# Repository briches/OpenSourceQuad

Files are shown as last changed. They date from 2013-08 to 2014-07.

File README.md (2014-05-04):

<b>OpenSourceQuad</b>
==========

<b>Author</b>: Brandon Riches<br />

Started in May of 2013, and always a work in progress! <br />

Feel free to <b>[fork](https://github.com/briches/OpenSourceQuad/fork)</b> the repo and submit a pull request.  

Released under the GNU Public License  

<b>Programming the flight controller:</b>  
----

(Finally) <b>Safe Fuse Bytes</b>  
<code>lfuse = 0xD6, hfuse = 0xB1, efuse = 0xfd</code>  

<b>Using arduino avrisp:</b>  
<code>avrdude -P comport -b 19200 -c avrisp -p m2560 -v -e -U flash:w:hexfilename.hex</code>  
<b>Using USBasp</b>  
<code>avrdude -c usbasp -p m2560 -v -e -U flash:w:tmp.hex</code>  
<b>Writing fuse bits</b>  
<code>avrdude -c usbasp -p m2560 -U hfuse:w:0xB1:m -U lfuse:w:0xD6:m -U efuse:w:0xFD:m</code>

<b>ESC Settings</b>  
- Batt Type: LiXX
- Cut off: high
- Cut off Type: hard
- Brake: off
- Timing: auto
- Start up: medium

Description
-----------

Quadcopter flight firmware! 

The end goal is to create future proof, easy-to-use 
and customizable firmware for any flight configuration ( which is quite the lofty goal, but I'm working on it).
<br /><br />

<br />
Sensors:
 - LSM303 Accelerometer / Magnetometer 
 - MPU3050 Gyro
 - Adafruit ultimate GPS module
 - Maxbotix USRF (LV-EZ1)
 - BMP085 Barometeric Pressure/Temperature/Altitude

Features and long term goals:
----------------------------
   <br />
  - Fully autonomous takeoff and landing. Has the option to be controlled via radio comms. <br />

  - 9DOF sensor module (IMU) with GPS and localization  <br />
  
  - Open source =]
   <br />
   <br />

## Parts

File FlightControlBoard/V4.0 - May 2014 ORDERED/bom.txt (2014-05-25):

Qty,Value,Device,Package,Parts,,,,Description,PROD_ID
4,LED,LED0603,LED-0603,"5_PWR, DIO1, HB, RSSI",,,,LEDs,
1,,M03LOCK,1X03_LOCK,USRF,,,,Header 3,
8,,PINHD-1X3,1X03,"M1, M2, M3, M4, SEL1, SEL2, SEL3, SEL4",,,,PIN HEADER,
1,500ma,PTCFUSE-1812,1812,F1,,,,"PTC fuses, resettable thermi",stors
1,0.22u,CAP0402-CAP,0402-CAP,C11,,,,Capacitor,
8,100n,CAP0402-CAP,0402-CAP,"C1, C2, C3, C4, C5, C","6,","C8,",C14,Capacitor,
4,10K,RESISTOR0402-RES,0402-RES,"R3, R18, R20, R24",,,,Resistor,
7,10k,RESISTOR0402-RES,0402-RES,"R9, R12, R15, R16, R1","9,",R22,", R23",Resistor,
1,10n,CAP0402-CAP,0402-CAP,C16,,,,Capacitor,
4,1K,RESISTOR0402-RES,0402-RES,"R1, R2, R5, R7",,,,Resistor,
1,1M,RESISTOR0402-RES,0402-RES,R8,,,,Resistor,
4,1k,RESISTOR0402-RES,0402-RES,"R4, R6, R13, R17",,,,Resistor,
4,4.7k,RESISTOR0402-RES,0402-RES,"R10, R11, R14, R21",,,,Resistor,
2,4.7u,C-EUC3216,C3216,"C12, C13",,,,"CAPACITOR, European symbol",
3,4.7u,CAP0402-CAP,0402-CAP,"C7, C9, C10",,,,Capacitor,
1,470n,CAP0402-CAP,0402-CAP,C15,,,,Capacitor,
1,ATMEGA2560AU,ATMEGA2560AU,TQFP100,U4,,,,Atmel 100-pin 8-bit uC,
1,AVR_SPI_PROG,AVR_SPI_PROG,AVR_ICSP,ICSP,,,,AVR 10-pin ICSP Header,
1,BMP085,BMP085,BMP085,BMP1,,,,BMP085 Pressure Sensor Great,little MEMS pressure sensor. SKU: COM-09603
8,ESC_CONN,ESC_CONN,ESC_CONN,"+, -, GND, U$3, U$4,",U$,"5, U","$6, V+",,
1,HEX_CONVERTER,HEX_CONVERTER,SO016,U2,,,,Just what it says.,
1,JST_XH_4,JST_XH_4,JST-XH4,JP1,,,,,
1,L3G4200D,L3G4200D,LGA16-4X4,U5,,,,"L3G4200D Three-axis, digital",output gyroscope
1,LS20031,LS20031,LS20031,U$1,,,,,
1,LSM303DLHSMD,LSM303DLHSMD,LGA28-5X5,U3,,,,I2C accelerometer/magnetomet,er/tilt compensated compass
6,MOSFET,MOSFET-NCHANNELBSS138,SOT23,"Q1, Q2, Q3, Q4, Q5, Q",6,,,Common NMOSFET Parts,TRANS-00830
1,NCP1117,NCP1117,DPAK,REG1,,,,,
1,RESONATOR,RESONATORMU,RESONATOR,CSTCE16MOV53-RO16MHZ,,,,,
2,SCHOTTKY-1206,D1206            SCHOTTKY-1206D1206,C1206,"D2, D3",,,,,
1,SWITCH-MOMENT,ARY-2-SMD-1101NE SWITCH-MOMENTARY-2-SMD-1101NE,TACTILE-SWITCH-1101NE,RST,,,,Various NO switches- pushbut,"tons, reed, etc"
1,USD-SOCKETNEW,USD-SOCKETNEW,MICRO-SD-SOCKET-PP,U1,,,,microSD Socket,
1,V_REG_LDOSMD,V_REG_LDOSMD,SOT23-5,1.8VREG,,,,Voltage Regulator LDO,
1,XBEE-1B3,XBEE-1B3,XBEE-SMD,U$2,,,,Xbee module footprints,CONN-09042
,,,,,,,,,
,,,,,,,,,
,Qty,Part Number,Manufacturer,Package,Reference,Description,Digi-Key P/N,Mouser P/N,Newark P/N
Capacitors,,,,,,,,,

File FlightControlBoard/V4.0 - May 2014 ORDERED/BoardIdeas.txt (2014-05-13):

Problems with V3.0
1. Board is pretty large - Made 7x7 cm
2. Trace width inconsistant
3. 3V3 Reg incorrectly routed
4. Servo leads incorrectly routed
5. Capacitor on 1.8V reg output
6. Barometeric sensor, make adaptable between BMP180 and BMP085
7. Include power connections on board!!

V3.1
Layers
Top. Normal Traces w/ GND Plane
Route2. Normal Traces w/ GND Plane
Route15. AGND Plane, no traces!
Bottom. +Vbatt Plane

Need to route GND planes around power connections
 - allow adequate spacing

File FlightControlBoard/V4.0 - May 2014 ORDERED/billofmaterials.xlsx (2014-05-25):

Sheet: bom_quadcopter
Quantity | Part | Optional | Approx. price per | Total
1 | Frame | 0 | $50.00 | $50.00
4 | Speed Controllers (ESC) | 0 | $15.00 | $60.00
4 | Motors, Brushless | 0 | $20.00 | $80.00
1 | Battery, LiPo | 0 | $40.00 | $40.00
4 | Propellors | 0 | $1.00 | $4.00
1 | Power distribution method | 0 | $5.00 | $5.00
1 | Control board | 0 | $100.00 | $100.00
1 | Ultrasonic range finder | 1 | $20.00 | $20.00
1 | Xbee Radio Module | 1 | $20.00 | $20.00
1 | GPS | 1 | $40.00 | $40.00
1 | microSD card | 1 | $15.00 | $15.00
 |  |  | Min | Max
 |  | Total | $339.00 | $434.00

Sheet: bom_board.xlsx
 | Bill of materials for Open Source Quad Control Board Rev 4. |  |  |  |  |  |  |  | PROD_ID
Capacitors
 | Quantity | Part | Value | Device | Package | Description | Digikey P/N | Manufacturer
 | 1 | C16 | 10nF | CAP0402-CAP | 402 | ceramic | 445-7386-1-ND | TDK Corporation
 | 10 | C1, C2, C3, C4, C5, C6, C8, C9, C14, C17 | 100nF | CAP0402-CAP | 402 | ceramic | 445-7348-1-ND | TDK Corporation
 | 1 | C11 | 220nF | CAP0402-CAP | 402 | ceramic | 445-5944-1-ND | TDK Corporation
 | 1 | C15 | 470n | CAP0402-CAP | 402 | ceramic | 445-10972-1-ND | TDK Corporation
 | 2 | C7, C10 | 4.7uF | CAP0402-CAP | 402 | ceramic | 445-10914-1-ND | TDK Corporation
 | 3 | C12, C13, C18 | 10uF | CAP_POL1206 | EIA3216 | polarized | 399-5152-1-ND | Kemet
Resistors
 | Quantity | Part | Value | Device | Package | Description | Digikey P/N | Manufacturer
 | 10 | R1, R2, R4, R5, R6, R7, R13, R17, R25, R26 | 1k | RESISTOR0603-RES | 603 | resistor | CR0603-JW-102ELFCT-ND | Bourns Inc.
 | 4 | R10, R11, R14, R21 | 4.7k | RESISTOR0603-RES | 603 | resistor | CR0603-JW-472ELFCT-ND | Bourns Inc.
 | 11 | R3, R9, R12, R15, R16, R18, R19, R20, R22, R23, R24 | 10k | RESISTOR0603-RES | 603 | resistor | CR0603-JW-103ELFCT-ND | Bourns Inc.
 | 1 | R8 | 1M | RESISTOR0603-RES | 603 | resistor | CR0603-JW-105ELFCT-ND | Bourns Inc.
Connectors
 | Quantity | Part | Value | Device | Package | Description | Digikey P/N | Manufacturer
 | 1 | 5x2 ICSP Header |  |  | 500 |  | 952-2380-ND | Harwin Inc.
 | 1 | SMT XH 4 pos connector |  |  | XH |  | 455-2262-1-ND | JST Sales America
 | 2 | Xbee header |  |  |  |  | S5751-10-ND | Sullins Connector
 | 1 | .1 " header 36 pos |  |  |  |  | WM50014-36-ND | Molex Inc.
 | 1 | CONN MINI MICRO-SD 8PIN PCB GOLD |  |  |  |  | 101-00660-68-6-1-ND | Amphenol Commer
 | 1 | CONN USB MINI B R/A SMD |  |  |  |  | ED2992CT-ND | On Shore
 | 4 | Jumper |  |  |  |  | 3M9580-ND | 3M4
Diodes
 | Quantity | Part | Value | Device | Package | Description | Digikey P/N | Manufacturer
 | 3 | HB, DIO1, RX | RED | LED0603 | 603 |  | 160-1436-1-ND | Lite-On Inc
 | 1 | TX | YELLOW | LED0603 | 603 |  | 160-1437-1-ND | Lite-On Inc
 | 2 | RSSI, 5_PWR | GREEN | LED0603 | 603 |  | 160-1435-1-ND | Lite-On Inc
 | 2 | SD1206 |  | SCHOTTKY-1206D1206 | 1206 |  | 478-7804-1-ND | AVX Corporation
Resonators
 | Quantity | Part | Value | Device | Package | Description | Digikey P/N | Manufacturer
 | 1 | CSTCE16M0V53-R0 | 20MHz |  | 3-SMD |  | 490-1198-1-ND | Murata
Fuses
 | Quantity | Part | Value | Device | Package | Description | Digikey P/N | Manufacturer
 | 1 | F1 | PTC_FUSE | PTCFUSE-1812 | 1812 |  | MF-MSMF050-2CT-ND | Bourns Inc.
MOSFETs
 | Quantity | Part | Value | Device | Package | Description | Digikey P/N | Manufacturer
 | 6 | Q1, Q2, Q3, Q4, Q5, Q6 | BSS | MOSFET-NCHANNELBSS138 | SOT23 |  | BSS138CT-ND | Fairchild Semi
Switch
 | Quantity | Part | Value | Device | Package | Description | Digikey P/N | Manufacturer
 | 1 | RST |  |  | TACTILE-SWITCH-1101NE |  | 401-1705-1-ND | C&K Components
IC's
 | Quantity | Part | Value | Device | Package | Description | Digikey P/N | Manufacturer
 | 1 | U7 | FT232RLSSOP |  | 28-SSOP | USB-RS232 | 768-1007-1-ND | FTDI
 | 1 | U5 | L3G4200D |  | LGA16-4X4 | gyro | 497-11071-1-ND | ST
 | 1 | U4 | ATMEGA2560AU | ATMEGA2560AU | TQFP100 | MCU | ATMEGA2560-16AU-ND | Atmel
 | 1 | U3 | LSM303DLHSMD |  | LGA28-5X5 |  | 497-10765-1-ND | ST
 | 1 | U2 | HEX_CONVERTER |  | 16-SOIC N | logic level | 296-31503-1-ND | TI
 | 1 | REG1 | NCP1117 |  | DPAK | 3.3V reg | NCP1117DT33RKGOSCT-ND | ON Semi
 | 1 | 1.8VREG | V_REG_LDOSMD |  | TSOT-23-5 | 1.8V reg | 296-17778-1-ND | TI
 | 1 | BMP085 | Pressure Sensor |  |  |  | N/A
 | 1 | XB24-API-001 | Xbee |  |  |  | 602-1273-ND
 | 1 | LS20031 | GPS

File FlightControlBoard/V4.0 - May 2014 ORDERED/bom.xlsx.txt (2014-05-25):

Capacitors															
	Quantity	Part	Value	Device	Package	Description	Part Number								PROD_ID
	1	C16	10nF	CAP0402-CAP	0402-CAP	Capacitor									
	10	"C1, C2, C3, C4, C5, C6, C8, C9, C14, C17"	100nF	CAP0402-CAP	402	ceramic									
	1	C11	220nF	CAP0402-CAP	402	ceramic									
	1	C15	470n	CAP0402-CAP											
	2	"C7, C10"	4.7uF	CAP0402-CAP	402	ceramic	445-10914-1-ND								
	3	"C12, C13, C18"	10uF	CAP_POL1206	EIA3216	polarized									

Resistors

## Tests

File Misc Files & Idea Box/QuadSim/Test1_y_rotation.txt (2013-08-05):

Test ID: 1.0

Total Mass: 1.1
Moments of Inertia: [0.0089, 0.0098, 0.0187]
Thrust: 0.15
Current Draw: [5, 18]
Battery Capacity: 2450
Rotational DoF axis: [0, 1, 0]
Translational DoF axis: [0, 0, 0]

This test is constrained to have only rotation about the y-axis,
as in our test apparatus. 
Most of these values are guesses still.

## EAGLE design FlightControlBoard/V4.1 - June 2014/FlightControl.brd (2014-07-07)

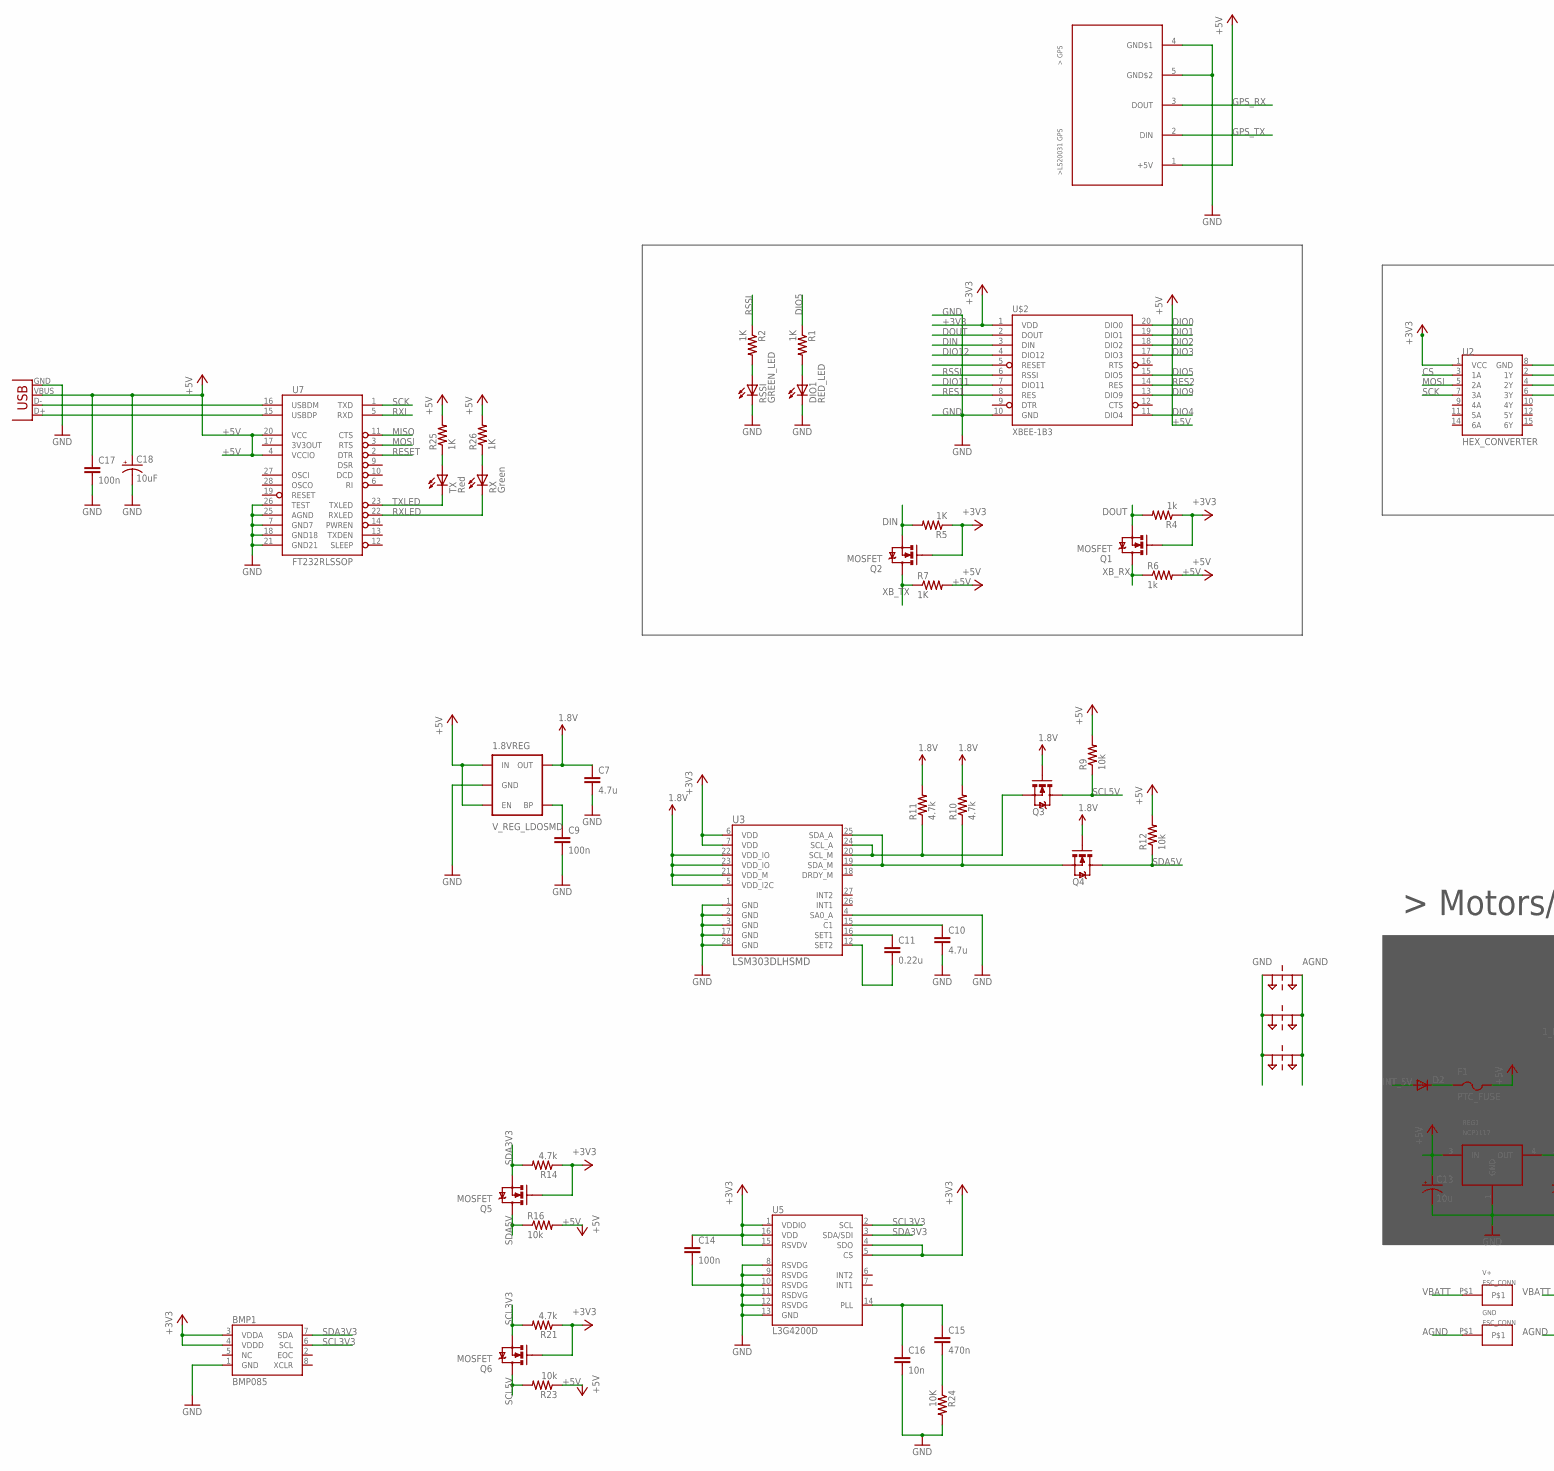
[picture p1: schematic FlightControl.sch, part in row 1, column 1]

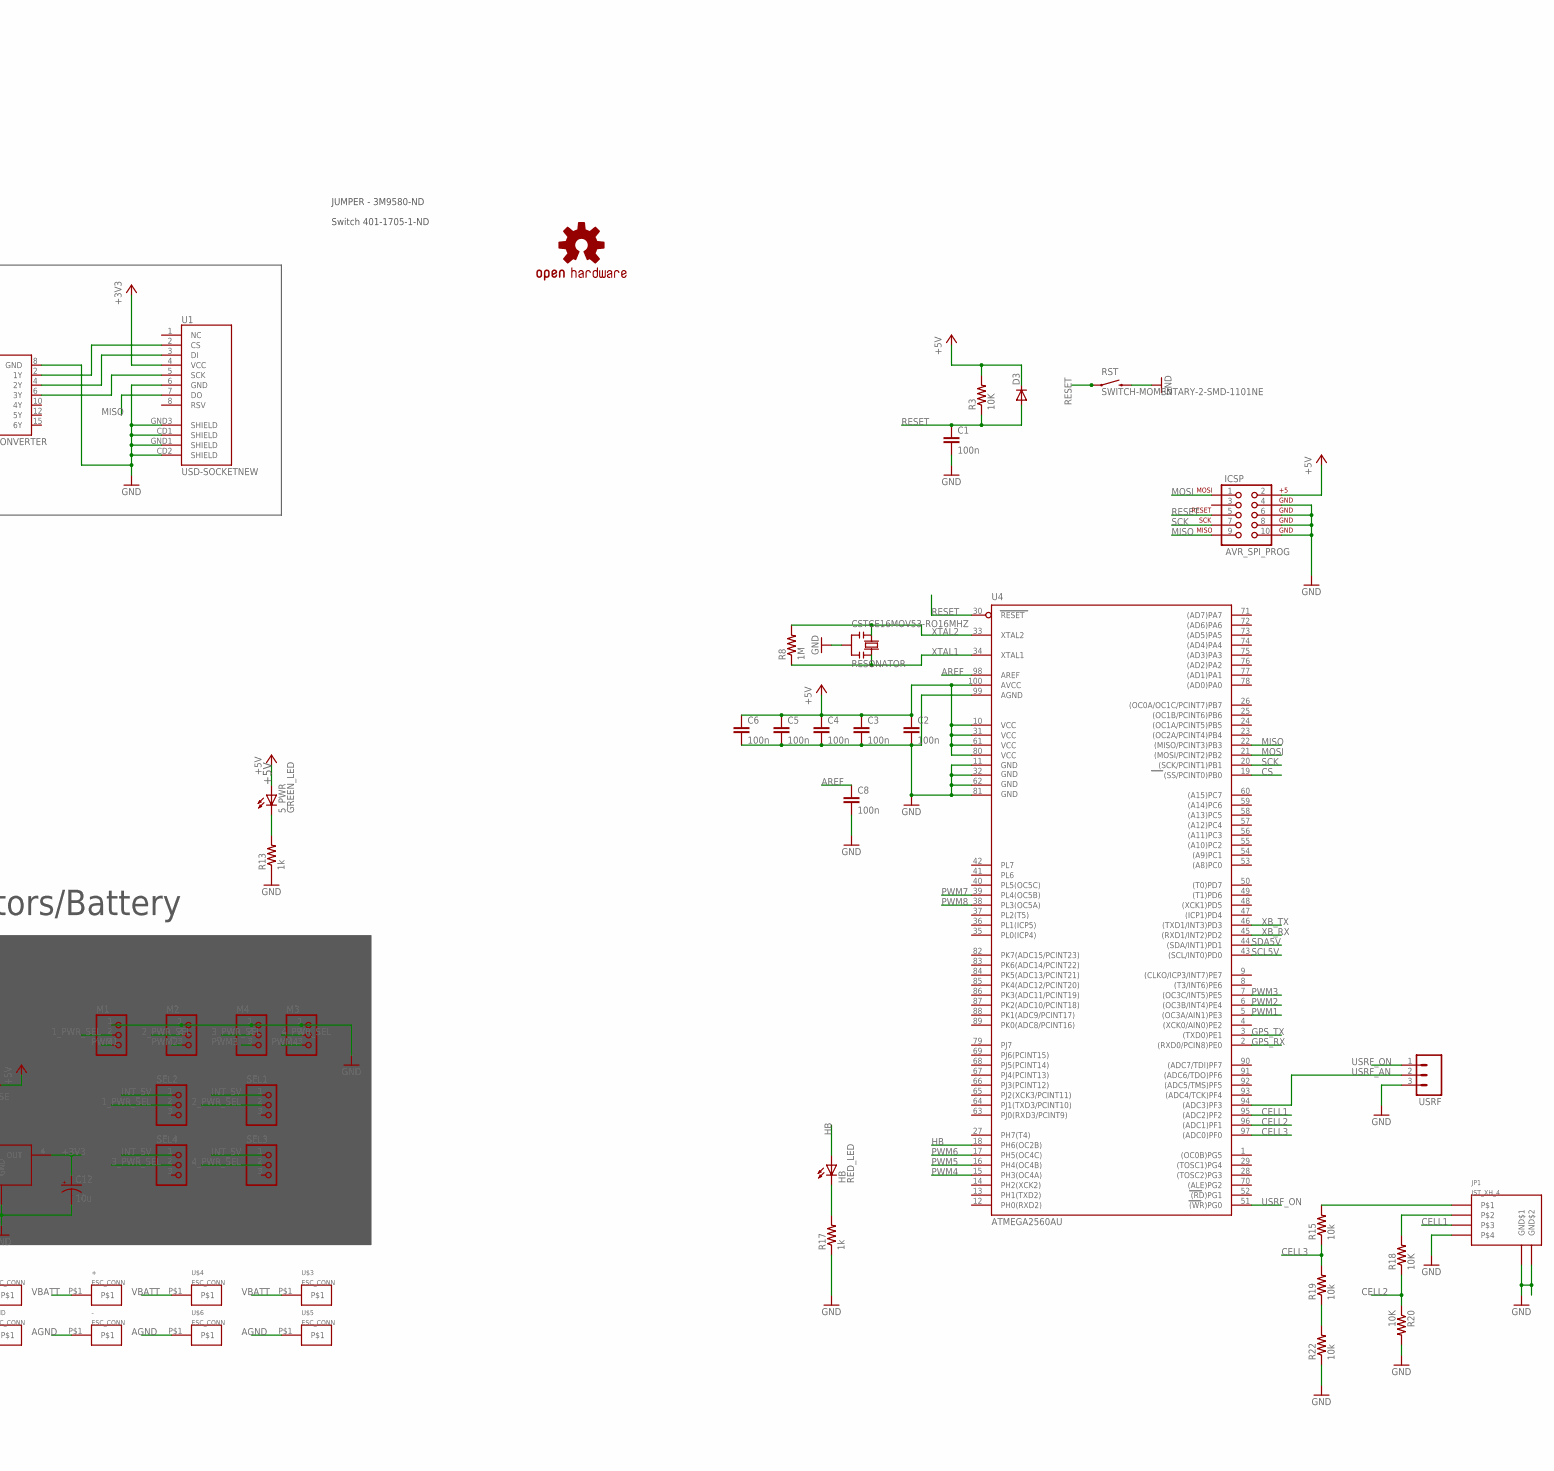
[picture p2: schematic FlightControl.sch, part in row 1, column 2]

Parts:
1.8VREG: V_REG_LDOSMD; SOT23-5
5_PWR: GREEN_LED; LED-0603
+: ESC_CONN
-: ESC_CONN
BMP1: BMP085
C1, C2, C3, C4, C5, C6, C8, C9, C14, C17: 100n; 0402-CAP
C7, C10: 4.7u; 0402-CAP
C11: 0.22u; 0402-CAP
C12, C13: 10u; EIA3216
C15: 470n; 0402-CAP
C16: 10n; 0402-CAP
C18: 10uF; EIA3216
CSTCE16MOV53-RO16MHZ: RESONATOR
D2, D3: SCHOTTKY-1206D1206; C1206
DIO1: RED_LED; LED-0603
F1: PTC_FUSE; 1812
GND: ESC_CONN
HB: RED_LED; LED-0603
ICSP: AVR_SPI_PROG; AVR_ICSP
JP1: JST_XH_4; JST-XH4
LOGO1: OSHW-LOGOL; OSHW-LOGO-L
M1, M2, M3, M4: PINHD-1X3; 1X03
PT1, PT2, PT3: 2PT_GND_TIE
Q1, Q2, Q3, Q4, Q5, Q6: MOSFET; SOT23
R1, R2, R5, R7, R25, R26: 1K; 0603-RES
R3, R18, R20, R24: 10K; 0603-RES
R4, R6, R13, R17: 1k; 0603-RES
R8: 1M; 0603-RES
R9, R12, R15, R16, R19, R22, R23: 10k; 0603-RES
R10: 4.7k; 0402-RES
R11, R14, R21: 4.7k; 0603-RES
REG1: NCP1117; DPAK
RSSI: GREEN_LED; LED-0603
RST: SWITCH-MOMENTARY-2-SMD-1101NE; TACTILE-SWITCH-1101NE
RX: Green; LED-0603
SEL1, SEL2, SEL3, SEL4: PINHD-1X3; 1X03
TX: Red; LED-0603
U1: USD-SOCKETNEW; MICRO-SD-SOCKET-PP
U2: HEX_CONVERTER; SO016
U3: LSM303DLHSMD; LGA28-5X5
U4: ATMEGA2560AU; TQFP100
U5: L3G4200D; LGA16-4X4
U7: FT232RLSSOP; SSOP28DB
U$1: LS20031
U$2: XBEE-1B3; XBEE-SMD
U$3, U$4, U$5, U$6: ESC_CONN
USRF: M03LOCK; 1X03_LOCK
V+: ESC_CONN
X2: USB-SMD-NS; USB-MINIB-NOSTOP

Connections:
1.8V: 1.8VREG.5 (OUT), C7.1, Q3.1 (G), Q4.1 (G), R10.2, R11.2, U3.5 (VDD_I2C), U3.21 (VDD_M), U3.22 (VDD_IO), U3.23 (VDD_IO)
1_PWR_SEL: M1.2, SEL2.2
2_PWR_SEL: M2.2, SEL1.2
3_PWR_SEL: M4.2, SEL4.2
4_PWR_SEL: M3.2, SEL3.2
+3V3: BMP1.3 (VDDA), BMP1.4 (VDDD), C12.A (+), C14.1, Q1.1 (G), Q2.1 (G), Q5.1 (G), Q6.1 (G), R4.1, R5.1, R14.1, R21.1, REG1.4 (OUT), U1.4 (VCC), U2.1 (VCC), U3.6 (VDD), U3.7 (VDD), U5.1 (VDDIO), U5.4 (SDO), U5.5 (CS), U5.15 (RSVDV), U5.16 (VDD), U$2.1 (VDD)
+5V: 1.8VREG.1 (IN), 1.8VREG.3 (EN), 5_PWR.A, C2.1, C3.1, C4.1, C5.1, C6.1, C13.A (+), C17.1, C18.A (+), D3.2 (C), F1.2, ICSP.2, R3.2, R6.2, R7.2, R9.2, R12.2, R16.2, R23.1, R25.2, R26.2, REG1.3 (IN), U4.10 (VCC), U4.31 (VCC1), U4.61 (VCC2), U4.80 (VCC3), U4.100 (AVCC), U7.4 (VCCIO), U7.20 (VCC), U$1.1 (+5V), X2.VBUS
AGND: -.P$1, GND.P$1, PT1.P$2, PT2.P$2, PT3.P$2, U$5.P$1, U$6.P$1
AREF: C8.1, U4.98 (AREF)
CELL1: JP1.P$3, U4.95 ((ADC2)PF2)
CELL2: R18.1, R20.1, U4.96 ((ADC1)PF1)
CELL3: R15.1, R19.2, U4.97 ((ADC0)PF0)
CS: U2.3 (1A), U4.19 ((SS/PCINT0)PB0)
DIN: Q2.2 (S), R5.2, U$2.3 (DIN)
DIO0: U$2.20 (DIO0)
DIO1: U$2.19 (DIO1)
DIO2: U$2.18 (DIO2)
DIO3: U$2.17 (DIO3)
DIO4: U$2.11 (DIO4)
DIO5: R1.1, U$2.15 (DIO5)
DIO9: U$2.13 (DIO9)
DIO11: U$2.7 (DIO11)
DIO12: U$2.4 (DIO12)
DOUT: Q1.2 (S), R4.2, U$2.2 (DOUT)
GND: 1.8VREG.2 (GND), BMP1.1 (GND), C1.2, C2.2, C3.2, C4.2, C5.2, C6.2, C7.2, C8.2, C9.2, C10.2, C12.C (-), C13.C (-), C14.2, C16.2, C17.2, C18.C (-), CSTCE16MOV53-RO16MHZ.2, DIO1.C, ICSP.4, ICSP.6, ICSP.8, ICSP.10, JP1.GND$1, JP1.GND$2, JP1.P$4, M1.1, M2.1, M3.1, M4.1, PT1.P$1, PT2.P$1, PT3.P$1, R13.1, R17.1, R20.2, R22.1, R24.2, REG1.1 (GND), RSSI.C, RST.P$2 (2), U1.6 (GND), U1.CD1 (SHIELD), U1.CD2 (SHIELD), U1.GND1 (SHIELD), U1.GND3 (SHIELD), U2.8 (GND), U3.1 (GND), U3.2 (GND), U3.3 (GND), U3.4 (SA0_A), U3.17 (GND), U3.28 (GND), U4.11 (GND), U4.32 (GND1), U4.62 (GND2), U4.81 (GND3), U4.99 (AGND), U5.8 (RSVDG), U5.9 (RSVDG), U5.10 (RSVDG), U5.11 (RSDVG), U5.12 (RSVDG), U5.13 (GND), U7.7 (GND7), U7.18 (GND18), U7.21 (GND21), U7.25 (AGND), U7.26 (TEST), U$1.4 (GND$1), U$1.5 (GND$2), U$2.10 (GND), USRF.3, X2.GND
GPS_RX: U4.2 ((RXD0/PCIN8)PE0), U$1.3 (DOUT)
GPS_TX: U4.3 ((TXD0)PE1), U$1.2 (DIN)
HB: HB.A, U4.18 (PH6(OC2B))
INT_5V: D2.1 (A), SEL1.1, SEL2.1, SEL3.1, SEL4.1
MISO: ICSP.9, U1.7 (DO), U4.22 ((MISO/PCINT3)PB3), U7.11 (CTS)
MOSI: ICSP.1, U2.5 (2A), U4.21 ((MOSI/PCINT2)PB2), U7.3 (RTS)
unnamed: R19.1, R22.2
unnamed: 1.8VREG.4 (BP), C9.1
unnamed: U1.2 (CS), U2.2 (1Y)
unnamed: U1.3 (DI), U2.4 (2Y)
unnamed: U1.5 (SCK), U2.6 (3Y)
unnamed: C11.1, U3.16 (SET1)
unnamed: 5_PWR.C, R13.2
unnamed: DIO1.A, R1.2
unnamed: R2.2, RSSI.A
unnamed: HB.C, R17.2
unnamed: R25.1, TX.A
unnamed: C11.2, U3.12 (SET2)
unnamed: C10.1, U3.15 (C1)
unnamed: D2.2 (C), F1.1
unnamed: Q3.2 (S), R11.1, U3.20 (SCL_M), U3.24 (SCL_A)
unnamed: Q4.2 (S), R10.1, U3.19 (SDA_M), U3.25 (SDA_A)
unnamed: JP1.P$2, R18.2
unnamed: C15.1, C16.1, U5.14 (PLL)
unnamed: C15.2, R24.1
unnamed: JP1.P$1, R15.2
unnamed: R26.1, RX.A
PWM1: M1.3, U4.5 ((OC3A/AIN1)PE3)
PWM2: M2.3, U4.6 ((OC3B/INT4)PE4)
PWM3: M4.3, U4.7 ((OC3C/INT5)PE5)
PWM4: M3.3, U4.15 (PH3(OC4A))
PWM5: U4.16 (PH4(OC4B))
PWM6: U4.17 (PH5(OC4C))
PWM7: U4.39 (PL4(OC5B))
PWM8: U4.38 (PL3(OC5A))
RES1: U$2.8 (RES)
RES2: U$2.14 (RES)
RESET: C1.1, D3.1 (A), ICSP.5, R3.1, RST.P$1 (1), U4.30 (RESET), U7.2 (DTR)
RSSI: R2.1, U$2.6 (RSSI)
RXI: U7.5 (RXD)
RXLED: RX.C, U7.22 (RXLED)
SCK: ICSP.7, U2.7 (3A), U4.20 ((SCK/PCINT1)PB1), U7.1 (TXD)
SCL3V3: BMP1.6 (SCL), Q6.2 (S), R21.2, U5.2 (SCL)
SCL5V: Q3.3 (D), Q6.3 (D), R9.1, R23.2, U4.43 ((SCL/INT0)PD0)
SDA3V3: BMP1.7 (SDA), Q5.2 (S), R14.2, U5.3 (SDA/SDI)
SDA5V: Q4.3 (D), Q5.3 (D), R12.1, R16.1, U4.44 ((SDA/INT1)PD1)
TXLED: TX.C, U7.23 (TXLED)
USB_D+: U7.15 (USBDP), X2.D+
USB_D-: U7.16 (USBDM), X2.D-
USRF_AN: U4.94 ((ADC3)PF3), USRF.2
USRF_ON: U4.51 ((WR)PG0), USRF.1
VBATT: +.P$1, U$3.P$1, U$4.P$1, V+.P$1
XB_RX: Q1.3 (D), R6.1, U4.45 ((RXD1/INT2)PD2)
XB_TX: Q2.3 (D), R7.1, U4.46 ((TXD1/INT3)PD3)
XTAL1: CSTCE16MOV53-RO16MHZ.3, R8.1, U4.34 (XTAL1)
XTAL2: CSTCE16MOV53-RO16MHZ.1, R8.2, U4.33 (XTAL2)

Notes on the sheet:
JUMPER - 3M9580-ND
Switch 401-1705-1-ND

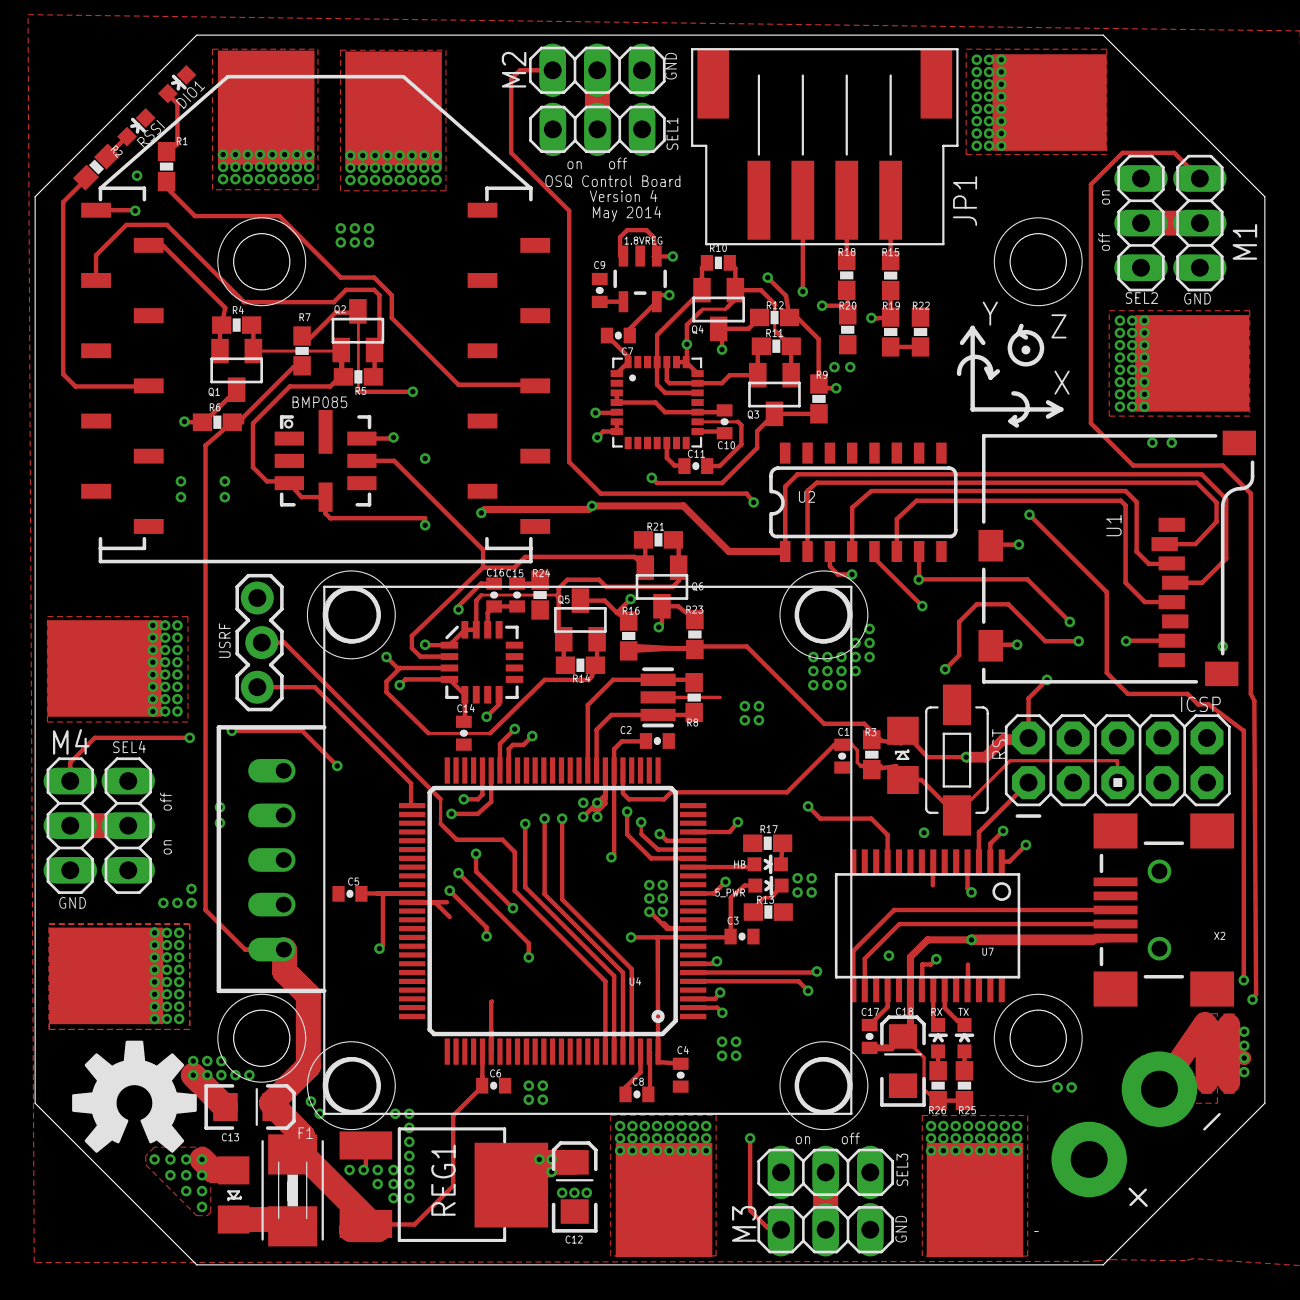
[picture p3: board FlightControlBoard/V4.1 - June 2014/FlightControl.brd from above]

Board: 4 copper layers, 70.0 x 70.0 mm, 96 parts (0 on the bottom side), 66 nets.

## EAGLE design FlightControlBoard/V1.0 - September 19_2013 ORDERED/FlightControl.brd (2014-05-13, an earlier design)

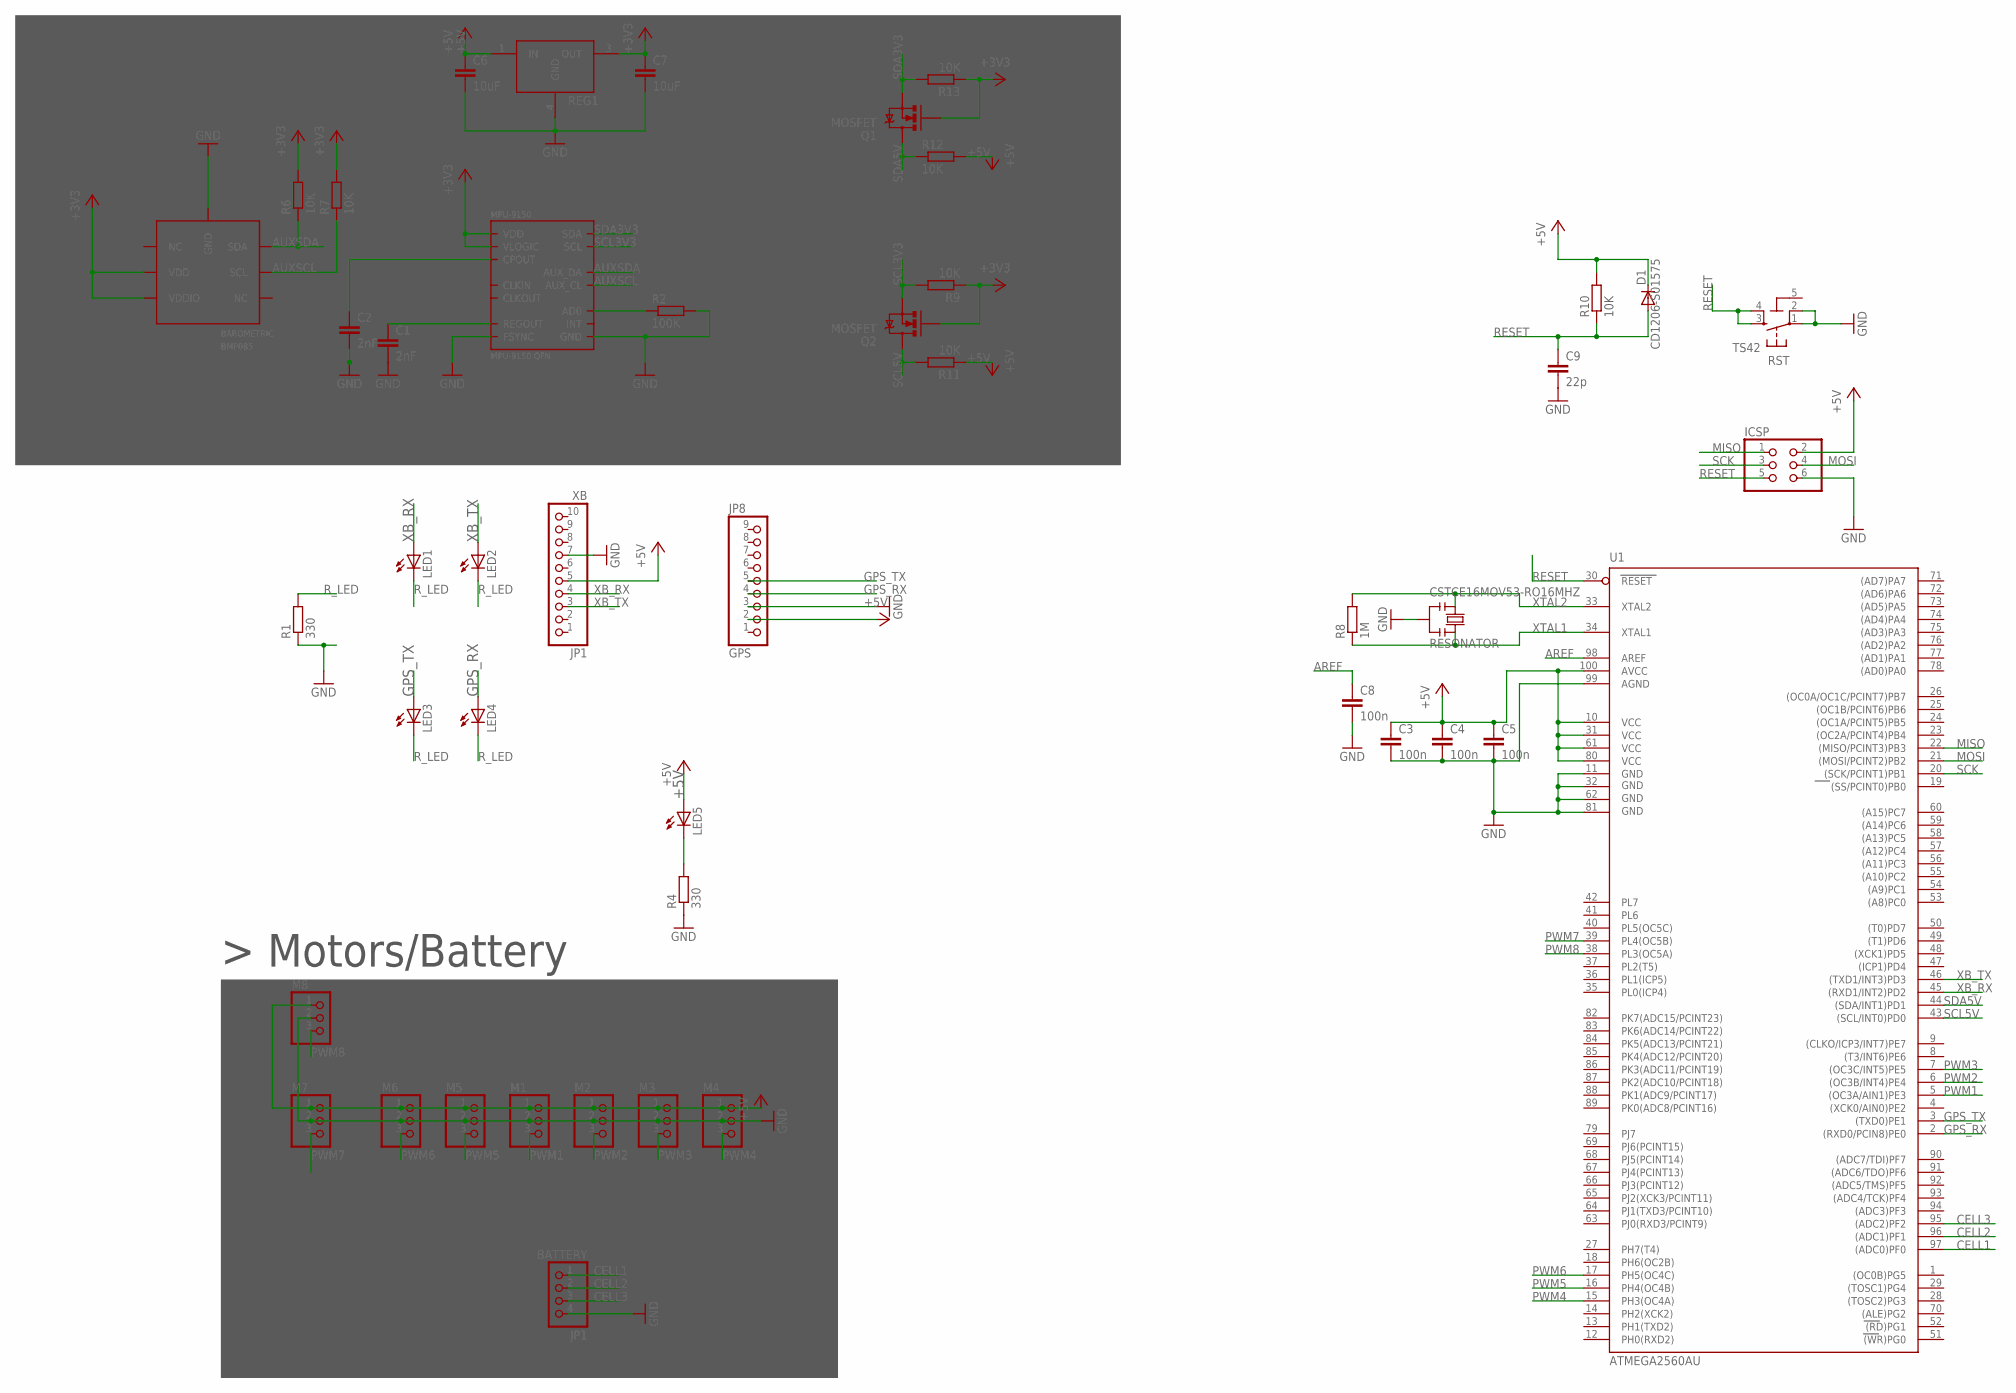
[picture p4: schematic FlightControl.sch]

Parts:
BAROMETRIC: BMP085; 7LGA
BATTERY: JP1; 1X04
C1, C2: 2nF; C0603-ROUND
C3, C4, C5, C8: 100n; C0603-ROUND
C6, C7: 10uF; CAP-PTH-SMALLEZ
C9: 22p; C0603-ROUND
CSTCE16MOV53-RO16MHZ: RESONATOR
D1: CD1206-S01575; MINIMELF
GPS: JP8; 1X09
ICSP: PINHD-2X3; 2X03
JP1: XB; 1X10
LED1, LED2, LED3, LED4, LED5: LEDCHIPLED_1206; CHIPLED_1206
M1, M2, M3, M4, M5, M6, M7, M8: PINHD-1X3; 1X03
MPU-9150: MPU-9150.QFN; QFN.24.4X4
Q1, Q2: MOSFET; SOT23
R1, R4: 330; R0603-ROUND
R2: 100K; R0603-ROUND
R6, R7, R9, R10, R11, R12, R13: 10K; R0603-ROUND
R8: 1M; R0603-ROUND
REG1: LD39300; DPAK
RST: TS42
U1: ATMEGA2560AU; TQFP100

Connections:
5-GND: RST.5 (5-GND)
+3V3: BAROMETRIC.2 (VDD), BAROMETRIC.3 (VDDIO), C7.1, MPU-9150.3 (VDD), MPU-9150.8 (VLOGIC), MPU-9150.13 (VDD), Q1.1 (G), Q2.1 (G), R6.2, R7.2, R9.1, R13.1, REG1.3 (OUT)
+5V: C3.1, C4.1, C5.1, C6.1, D1.C, GPS.2, ICSP.2, JP1.5, LED5.A, M1.1, M2.1, M3.1, M4.1, M5.1, M6.1, M7.1, M8.1, R10.2, R11.1, R12.2, REG1.1 (IN), U1.10 (VCC), U1.31 (VCC1), U1.61 (VCC2), U1.80 (VCC3), U1.100 (AVCC)
AD0: MPU-9150.9 (AD0), R2.1
AREF: C8.1, U1.98 (AREF)
AUXSCL: BAROMETRIC.5 (SCL), MPU-9150.7 (AUX_CL), R7.1
AUXSDA: BAROMETRIC.6 (SDA), MPU-9150.6 (AUX_DA), R6.1
CELL1: BATTERY.1, U1.97 ((ADC0)PF0)
CELL2: BATTERY.2, U1.96 ((ADC1)PF1)
CELL3: BATTERY.3, U1.95 ((ADC2)PF2)
CPOUT: C2.1, MPU-9150.20 (CPOUT)
GND: BAROMETRIC.7 (GND), BATTERY.4, C1.2, C2.2, C3.2, C4.2, C5.2, C6.2, C7.2, C8.2, C9.2, CSTCE16MOV53-RO16MHZ.2, GPS.3, ICSP.6, JP1.7, M1.2, M2.2, M3.2, M4.2, M5.2, M6.2, M7.2, M8.2, MPU-9150.11 (FSYNC), MPU-9150.15 (GND), MPU-9150.17 (GND), MPU-9150.18 (GND), R1.1, R2.2, R4.1, REG1.4 (GND), RST.1, RST.2, U1.11 (GND), U1.32 (GND1), U1.62 (GND2), U1.81 (GND3), U1.99 (AGND)
GPS_RX: GPS.4, LED4.A, U1.2 ((RXD0/PCIN8)PE0)
GPS_TX: GPS.5, LED3.A, U1.3 ((TXD0)PE1)
MISO: ICSP.1, U1.22 ((MISO/PCINT3)PB3)
MOSI: ICSP.4, U1.21 ((MOSI/PCINT2)PB2)
unnamed: LED5.C, R4.2
PWM1: M1.3, U1.5 ((OC3A/AIN1)PE3)
PWM2: M2.3, U1.6 ((OC3B/INT4)PE4)
PWM3: M3.3, U1.7 ((OC3C/INT5)PE5)
PWM4: M4.3, U1.15 (PH3(OC4A))
PWM5: M5.3, U1.16 (PH4(OC4B))
PWM6: M6.3, U1.17 (PH5(OC4C))
PWM7: M7.3, U1.39 (PL4(OC5B))
PWM8: M8.3, U1.38 (PL3(OC5A))
REGOUT: C1.1, MPU-9150.10 (REGOUT)
RESET: C9.1, D1.A, ICSP.5, R10.1, RST.3, RST.4, U1.30 (RESET)
R_LED: LED1.C, LED2.C, LED3.C, LED4.C, R1.2
SCK: ICSP.3, U1.20 ((SCK/PCINT1)PB1)
SCL3V3: MPU-9150.23 (SCL), Q2.2 (S), R9.2
SCL5V: Q2.3 (D), R11.2, U1.43 ((SCL/INT0)PD0)
SDA3V3: MPU-9150.24 (SDA), Q1.2 (S), R13.2
SDA5V: Q1.3 (D), R12.1, U1.44 ((SDA/INT1)PD1)
XB_RX: JP1.4, LED1.A, U1.45 ((RXD1/INT2)PD2)
XB_TX: JP1.3, LED2.A, U1.46 ((TXD1/INT3)PD3)
XTAL1: CSTCE16MOV53-RO16MHZ.3, R8.1, U1.34 (XTAL1)
XTAL2: CSTCE16MOV53-RO16MHZ.1, R8.2, U1.33 (XTAL2)

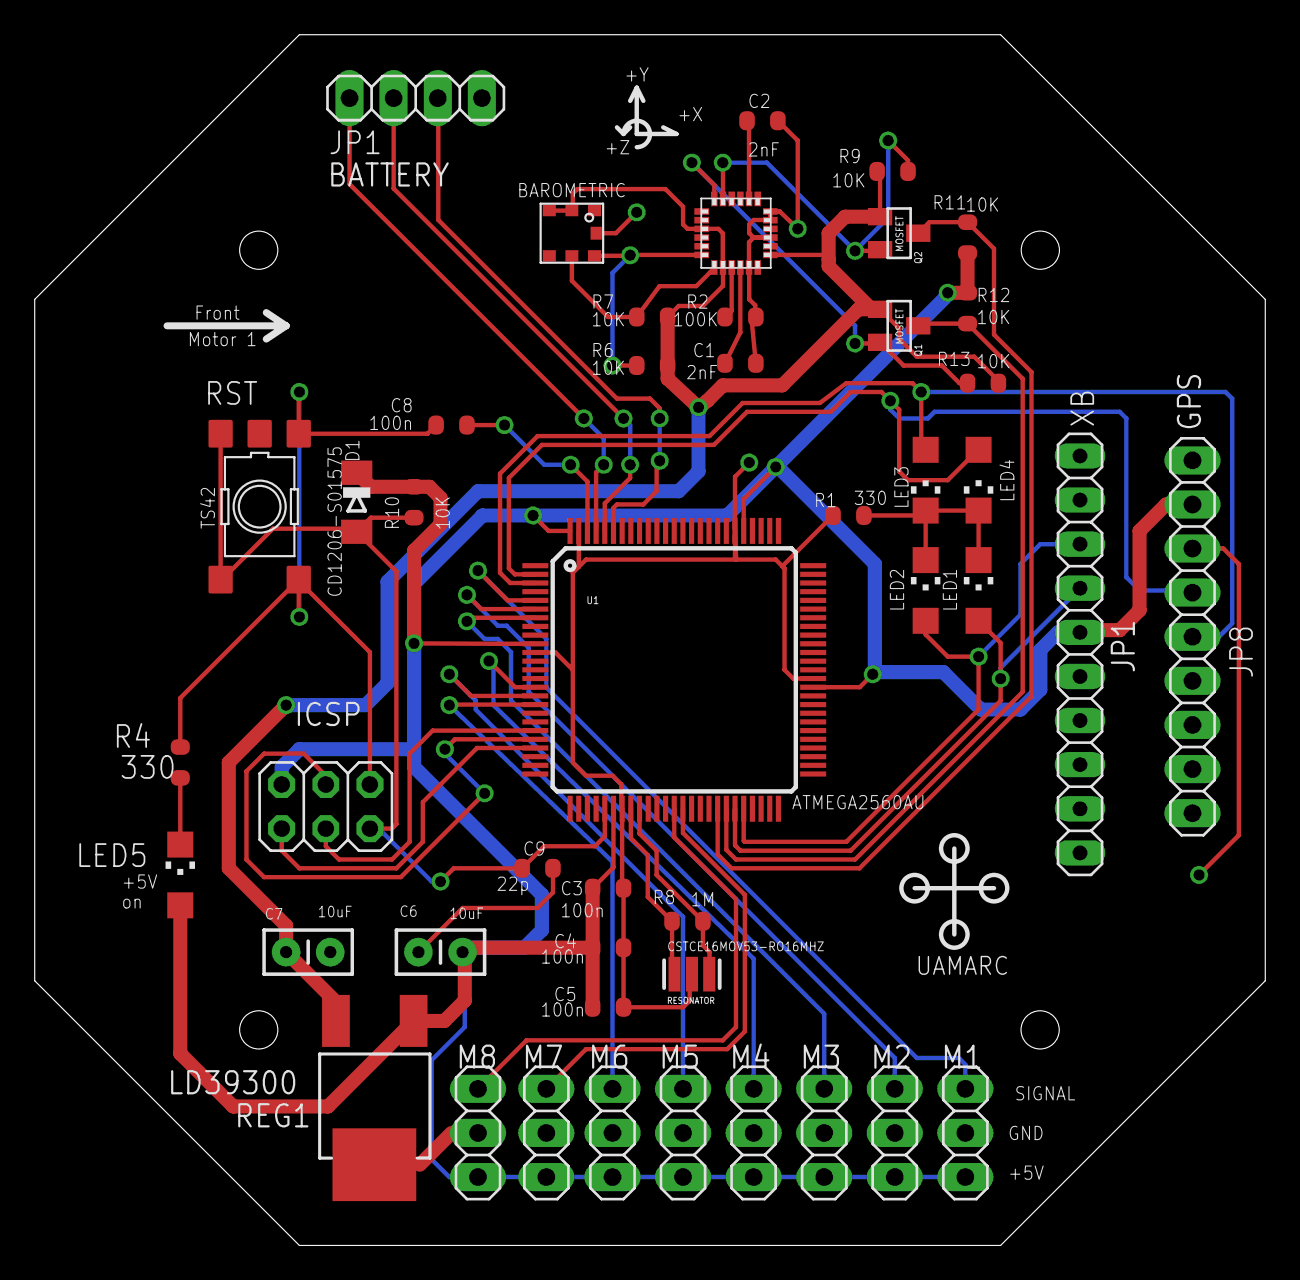
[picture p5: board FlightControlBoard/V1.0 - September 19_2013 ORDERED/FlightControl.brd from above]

Board: 2 copper layers, 70.9 x 69.7 mm, 46 parts (0 on the bottom side), 36 nets.

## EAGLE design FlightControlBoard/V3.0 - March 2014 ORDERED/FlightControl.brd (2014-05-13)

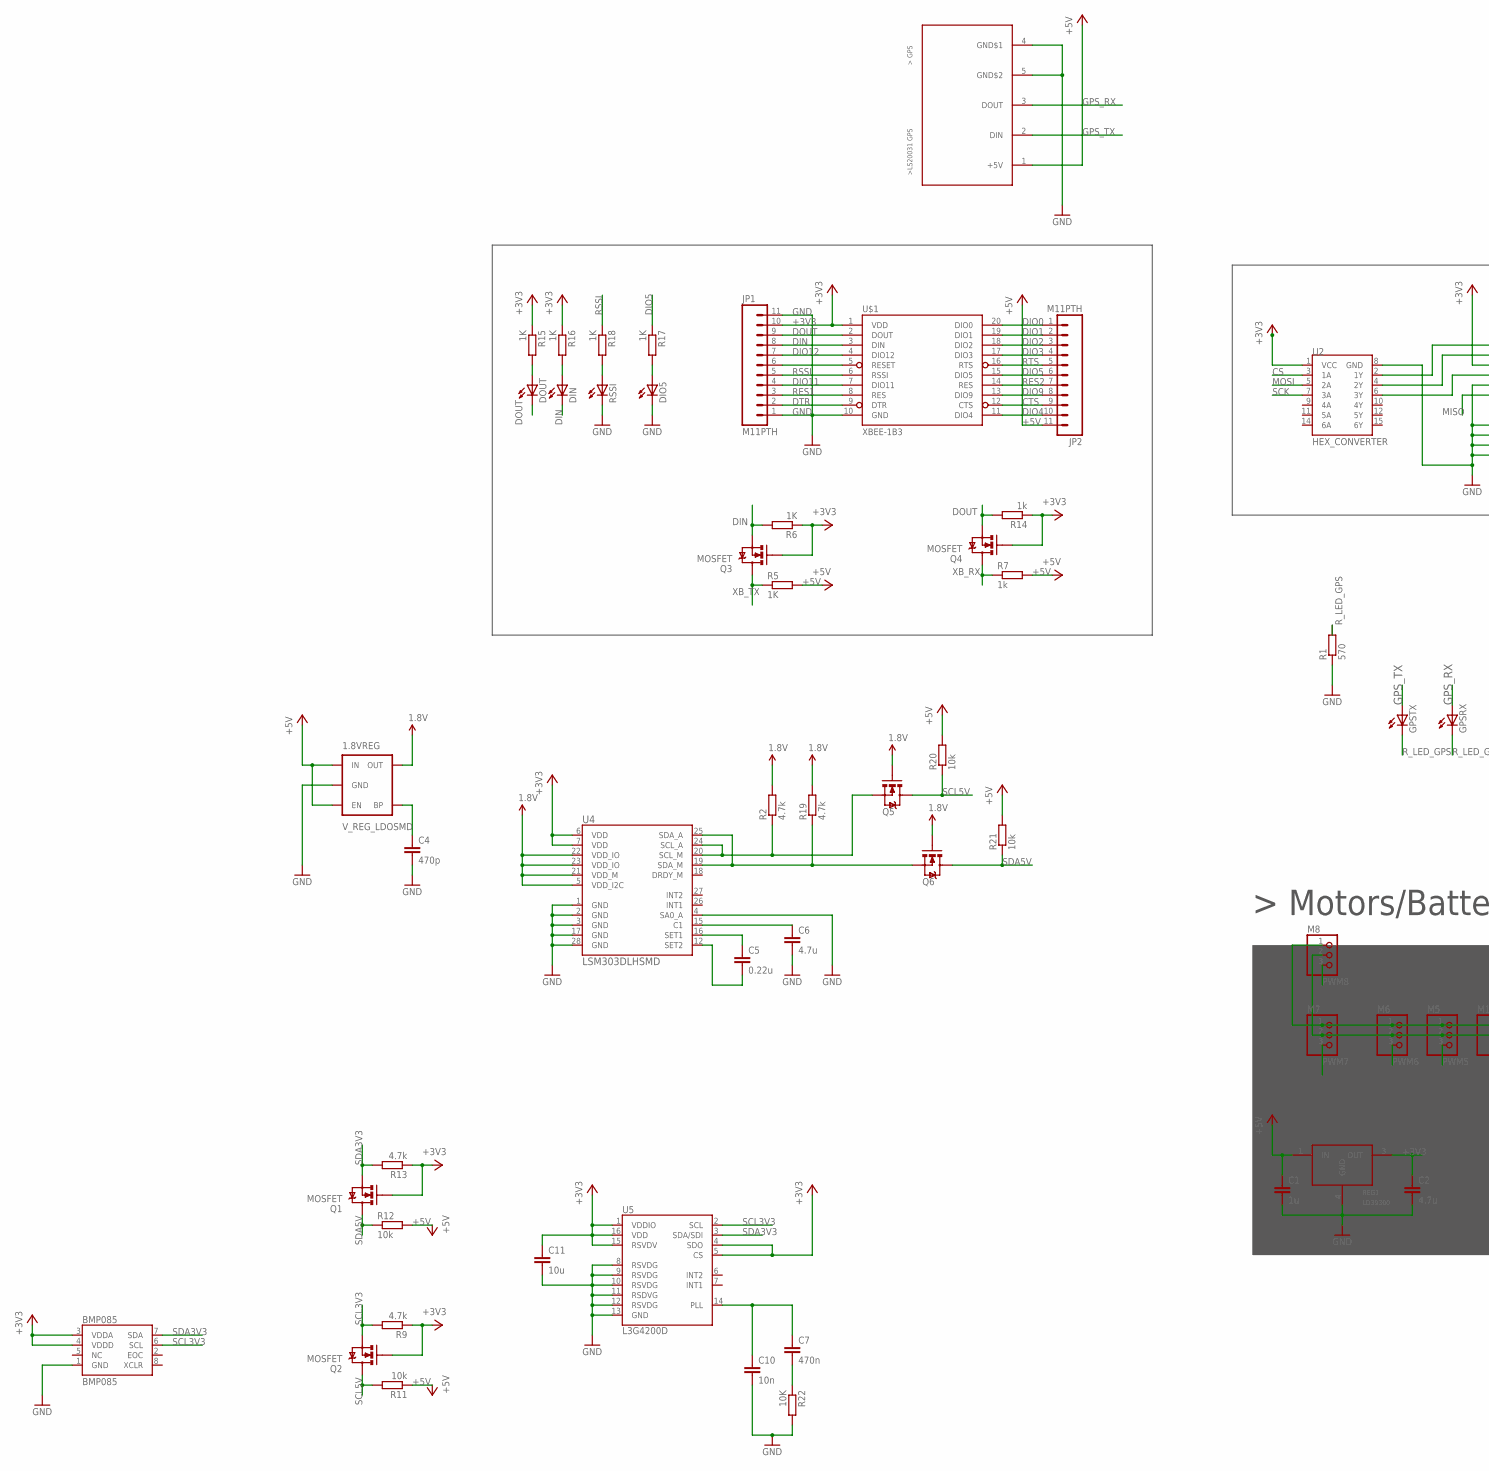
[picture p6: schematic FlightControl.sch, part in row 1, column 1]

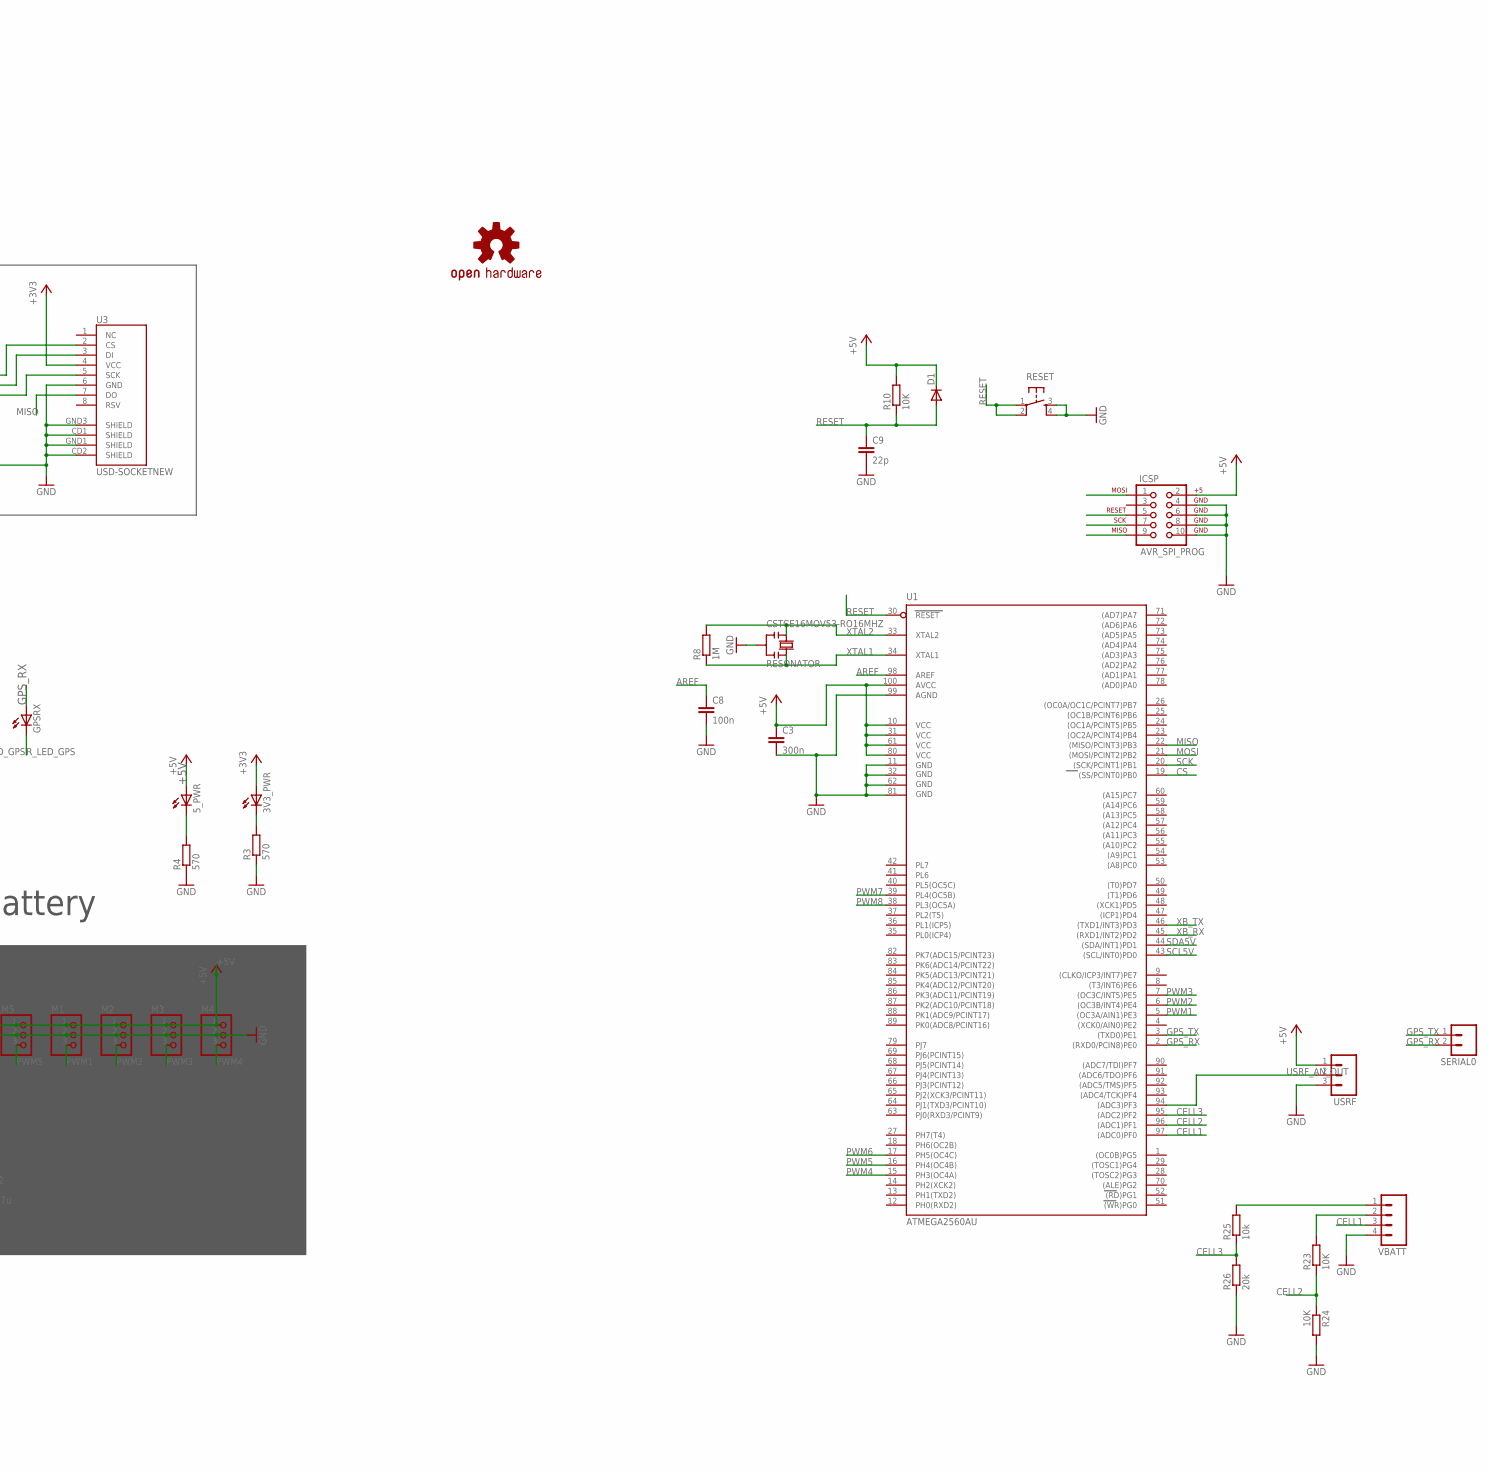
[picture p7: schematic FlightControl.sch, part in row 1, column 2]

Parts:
1.8VREG: V_REG_LDOSMD; SOT23-5
3V3_PWR, 5_PWR: LEDCHIPLED_1206; CHIPLED_1206
BMP085: BMP085
C1: 1u; C3216
C2, C6: 4.7u; C3216
C3: 300n; C3216
C4: 470p; C3216
C5: 0.22u; C3216
C7: 470n; C3216
C8: 100n; C3216
C9: 22p; C3216
C10: 10n; C3216
C11: 10u; C3216
CSTCE16MOV53-RO16MHZ: RESONATOR
D1: DIODE-MINIMELF; MINIMELF
DIN: LEDCHIPLED_1206; CHIPLED_1206
DIO5: LEDCHIPLED_1206; CHIPLED_1206
DOUT: LEDCHIPLED_1206; CHIPLED_1206
GPSRX: LEDCHIPLED_1206; CHIPLED_1206
GPSTX: LEDCHIPLED_1206; CHIPLED_1206
ICSP: AVR_SPI_PROG; AVR_ICSP
JP1, JP2: M11PTH; 1X11
LOGO1: OSHW-LOGOL; OSHW-LOGO-L
M1, M2, M3, M4, M5, M6, M7, M8: PINHD-1X3; 1X03
Q1, Q2, Q3, Q4, Q5, Q6: MOSFET; SOT23
R1, R3, R4: 570; R1206
R2, R9, R13, R19: 4.7k; R1206
R5, R6, R15, R16, R17, R18: 1K; R1206
R7, R14: 1k; R1206
R8: 1M; R1206
R10, R22, R23, R24: 10K; R1206
R11, R12, R20, R21, R25: 10k; R1206
R26: 20k; R1206
REG1: LD39300; DPAK
RESET: TAC_SWITCHPTH; TACTILE-PTH
RSSI: LEDCHIPLED_1206; CHIPLED_1206
SERIAL0: M02LOCK_LONGPADS; 1X02_LOCK_LONGPADS
U1: ATMEGA2560AU; TQFP100
U2: HEX_CONVERTER; SO016
U3: USD-SOCKETNEW; MICRO-SD-SOCKET-PP
U4: LSM303DLHSMD; LGA28-5X5
U5: L3G4200D; LGA16-4X4
U$1: XBEE-1B3; XBEE-SMD
U$2: LS20031
USRF: M03LONGPADS; 1X03_LONGPADS
VBATT: M04LONGPADS; 1X04_LONGPADS

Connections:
1.8V: 1.8VREG.5 (OUT), Q5.1 (G), Q6.1 (G), R2.2, R19.2, U4.5 (VDD_I2C), U4.21 (VDD_M), U4.22 (VDD_IO), U4.23 (VDD_IO)
+3V3: 3V3_PWR.A, BMP085.3 (VDDA), BMP085.4 (VDDD), C2.1, C11.1, JP1.10, Q1.1 (G), Q2.1 (G), Q3.1 (G), Q4.1 (G), R6.1, R9.1, R13.1, R14.1, R15.1, R16.1, REG1.3 (OUT), U2.1 (VCC), U3.4 (VCC), U4.6 (VDD), U4.7 (VDD), U5.1 (VDDIO), U5.4 (SDO), U5.5 (CS), U5.15 (RSVDV), U5.16 (VDD), U$1.1 (VDD)
+5V: 1.8VREG.1 (IN), 1.8VREG.3 (EN), 5_PWR.A, C1.1, C3.1, D1.C, ICSP.2, JP2.11, M1.1, M2.1, M3.1, M4.1, M5.1, M6.1, M7.1, M8.1, R5.2, R7.2, R10.2, R11.1, R12.2, R20.2, R21.2, REG1.1 (IN), U1.10 (VCC), U1.31 (VCC1), U1.61 (VCC2), U1.80 (VCC3), U1.100 (AVCC), U$2.1 (+5V), USRF.1
AREF: C8.1, U1.98 (AREF)
CELL1: U1.97 ((ADC0)PF0), VBATT.3
CELL2: R23.1, R24.1, U1.96 ((ADC1)PF1)
CELL3: R25.1, R26.2, U1.95 ((ADC2)PF2)
CS: U1.19 ((SS/PCINT0)PB0), U2.3 (1A)
CTS: JP2.9, U$1.12 (CTS)
DIN: DIN.C, JP1.8, Q3.2 (S), R6.2, U$1.3 (DIN)
DIO0: JP2.1, U$1.20 (DIO0)
DIO1: JP2.2, U$1.19 (DIO1)
DIO2: JP2.3, U$1.18 (DIO2)
DIO3: JP2.4, U$1.17 (DIO3)
DIO4: JP2.10, U$1.11 (DIO4)
DIO5: JP2.6, R17.1, U$1.15 (DIO5)
DIO9: JP2.8, U$1.13 (DIO9)
DIO11: JP1.4, U$1.7 (DIO11)
DIO12: JP1.7, U$1.4 (DIO12)
DOUT: DOUT.C, JP1.9, Q4.2 (S), R14.2, U$1.2 (DOUT)
DTR: JP1.2, U$1.9 (DTR)
GND: 1.8VREG.2 (GND), BMP085.1 (GND), C1.2, C2.2, C3.2, C4.2, C6.2, C8.2, C9.2, C10.2, C11.2, CSTCE16MOV53-RO16MHZ.2, DIO5.C, ICSP.4, ICSP.6, ICSP.8, ICSP.10, JP1.1, JP1.11, M1.2, M2.2, M3.2, M4.2, M5.2, M6.2, M7.2, M8.2, R1.1, R3.1, R4.1, R22.2, R24.2, R26.1, REG1.4 (GND), RESET.3, RESET.4, RSSI.C, U1.11 (GND), U1.32 (GND1), U1.62 (GND2), U1.81 (GND3), U1.99 (AGND), U2.8 (GND), U3.6 (GND), U3.CD1 (SHIELD), U3.CD2 (SHIELD), U3.GND1 (SHIELD), U3.GND3 (SHIELD), U4.1 (GND), U4.2 (GND), U4.3 (GND), U4.4 (SA0_A), U4.17 (GND), U4.28 (GND), U5.8 (RSVDG), U5.9 (RSVDG), U5.10 (RSVDG), U5.11 (RSDVG), U5.12 (RSVDG), U5.13 (GND), U$1.10 (GND), U$2.4 (GND$1), U$2.5 (GND$2), USRF.3, VBATT.4
GPS_RX: GPSRX.A, SERIAL0.2, U1.2 ((RXD0/PCIN8)PE0), U$2.3 (DOUT)
GPS_TX: GPSTX.A, SERIAL0.1, U1.3 ((TXD0)PE1), U$2.2 (DIN)
MISO: ICSP.9, U1.22 ((MISO/PCINT3)PB3), U3.7 (DO)
MOSI: ICSP.1, U1.21 ((MOSI/PCINT2)PB2), U2.5 (2A)
unnamed: 3V3_PWR.C, R3.2
unnamed: 1.8VREG.4 (BP), C4.1
unnamed: U2.2 (1Y), U3.2 (CS)
unnamed: U2.4 (2Y), U3.3 (DI)
unnamed: U2.6 (3Y), U3.5 (SCK)
unnamed: C5.1, U4.16 (SET1)
unnamed: 5_PWR.C, R4.2
unnamed: DIO5.A, R17.2
unnamed: R18.2, RSSI.A
unnamed: DIN.A, R16.2
unnamed: DOUT.A, R15.2
unnamed: JP1.6, U$1.5 (RESET)
unnamed: C5.2, U4.12 (SET2)
unnamed: C6.1, U4.15 (C1)
unnamed: Q5.2 (S), R2.1, U4.20 (SCL_M), U4.24 (SCL_A)
unnamed: Q6.2 (S), R19.1, U4.19 (SDA_M), U4.25 (SDA_A)
unnamed: R23.2, VBATT.2
unnamed: C7.1, C10.1, U5.14 (PLL)
unnamed: C7.2, R22.1
unnamed: R25.2, VBATT.1
PWM1: M1.3, U1.5 ((OC3A/AIN1)PE3)
PWM2: M2.3, U1.6 ((OC3B/INT4)PE4)
PWM3: M3.3, U1.7 ((OC3C/INT5)PE5)
PWM4: M4.3, U1.15 (PH3(OC4A))
PWM5: M5.3, U1.16 (PH4(OC4B))
PWM6: M6.3, U1.17 (PH5(OC4C))
PWM7: M7.3, U1.39 (PL4(OC5B))
PWM8: M8.3, U1.38 (PL3(OC5A))
RES1: JP1.3, U$1.8 (RES)
RES2: JP2.7, U$1.14 (RES)
RESET: C9.1, D1.A, ICSP.5, R10.1, RESET.1, RESET.2, U1.30 (RESET)
RSSI: JP1.5, R18.1, U$1.6 (RSSI)
RTS: JP2.5, U$1.16 (RTS)
R_LED_GPS: GPSRX.C, GPSTX.C, R1.2
SCK: ICSP.7, U1.20 ((SCK/PCINT1)PB1), U2.7 (3A)
SCL3V3: BMP085.6 (SCL), Q2.2 (S), R9.2, U5.2 (SCL)
SCL5V: Q2.3 (D), Q5.3 (D), R11.2, R20.1, U1.43 ((SCL/INT0)PD0)
SDA3V3: BMP085.7 (SDA), Q1.2 (S), R13.2, U5.3 (SDA/SDI)
SDA5V: Q1.3 (D), Q6.3 (D), R12.1, R21.1, U1.44 ((SDA/INT1)PD1)
USRF_AN_OUT: U1.94 ((ADC3)PF3), USRF.2
XB_RX: Q4.3 (D), R7.1, U1.45 ((RXD1/INT2)PD2)
XB_TX: Q3.3 (D), R5.1, U1.46 ((TXD1/INT3)PD3)
XTAL1: CSTCE16MOV53-RO16MHZ.3, R8.1, U1.34 (XTAL1)
XTAL2: CSTCE16MOV53-RO16MHZ.1, R8.2, U1.33 (XTAL2)

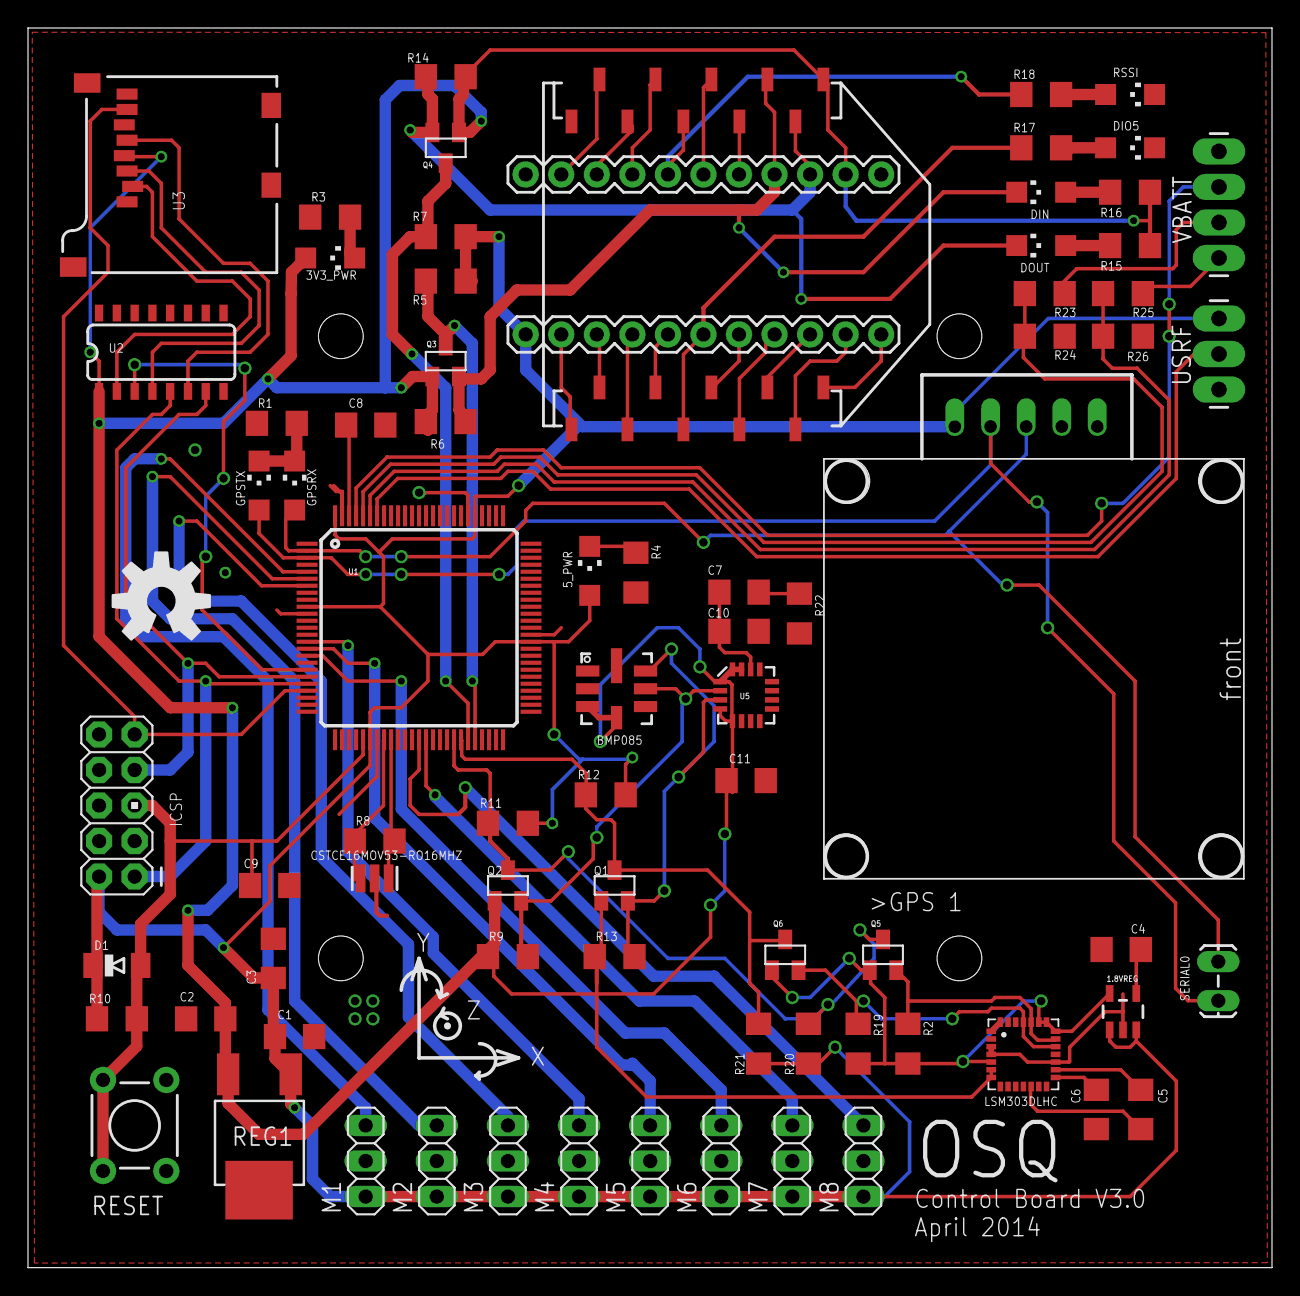
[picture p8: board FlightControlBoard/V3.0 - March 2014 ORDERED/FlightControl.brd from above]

Board: 2 copper layers, 88.9 x 88.6 mm, 79 parts (0 on the bottom side), 70 nets.

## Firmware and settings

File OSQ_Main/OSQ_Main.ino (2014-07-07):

/*=====================================================================
     osq_main
     OpenSourceQuad
     -------------------------------------------------------------------*/
/*================================================================================
 
     Author		: Brandon Riches
     Date		: August 2013
     License		: GNU Public License

     Main file for the OpenSourceQuad flight control firmware

     Copyright (C) 2013  Brandon Riches

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
     -----------------------------------------------------------------------------*/
#include "kinematics.h"
#include "IMU.h"
#include "quadcopter.h"
#include "motors.h"
#include "BMP085.h"
#include "nowire.h"
#include "GPS.h"
#include "altitudeprocessor.h"
#include "batterymanager.h"
#include "PID.h"
#include "EEPROM.h"

#include <Adafruit_GPS.h>         
#include <SoftwareSerial.h>
#include <Wire.h>
#include <SD.h>
#include <OSQ_Queue.h>

/** Program Specifications **/
int softwareVersionMajor;
int softwareVersionMinor;
long int flightNumber;
uint64_t cycleCount;
bool receivedStartupCommand = false;

/*=========================================================================
 Serial debugger options
 -----------------------------------------------------------------------*/
#define serialDebug        // <- Must be defined to use any of the other debuggers
//#define attitudeDebug     
//#define altitudeDebug
#define rx_txDebug
//#define autoBroadcast
//#define motorsDebug
#define sdDebug
//#define rollPIDdebug
//#define pitchPIDdebug
//#define yawPIDdebug
//#define altPIDdebug
//#define batteryDebug
//#define GPSDebug

/*=========================================================================
 Hardware options
 -----------------------------------------------------------------------*/
//** Battery **/
#define LIPO_3s
//#define 4sLIPO

/*=========================================================================
 Attitude offset calibration
 -----------------------------------------------------------------------*/
// Comment this line to use previously calibrated measurements
//#define newSensorOffsets
#define usePreviousOffsets

/** Math related definitions **/
#define Pi (3.14159265359F) // Its pi.

/*=========================================================================
 Sensor analog pins 
 -----------------------------------------------------------------------*/
#define USRF_PIN (3)        

/*=========================================================================
 SD logging definitions 
 -----------------------------------------------------------------------*/
char logFilename[12];
File logFile;

/*=========================================================================
 scanTelemetry()
 Watches for new commands sent via radio
 -----------------------------------------------------------------------*/
bool gotPID = false;
void scanTelemetry()
{
    unsigned char packet[5] = {
        0xFF, 0x00, 0x00, 0x00, 0x00    };
    int EEPROMselectionPID;

    switch(receiver.ScanForMessages())
    {
    case err:
        {
        }
        break;

    case disarm:
        {
            #ifdef serialDebug
                #ifdef rx_txDebug
                            Serial.println("Received DISARM command!");
                #endif
            #endif

            motorControl.motorDISARM();
            logFile.close();
            while(1);
        }
        break;

    case autoland:
        {
            #ifdef serialDebug
                #ifdef rx_txDebug
                            Serial.println("Received auto-land command!");
                #endif
            #endif

            // Auto-land
        }
        break;

    case start:
        {
            #ifdef serialDebug
                #ifdef rx_txDebug
                            Serial.println("Received start command!");
                #endif
            #endif

            receivedStartupCommand = true;
        }
        break;

    case broadcastData:
        {
            #ifdef serialDebug
                #ifdef rx_txDebug
                            Serial.println("Received broadcast data command!");
                #endif
            #endif
            // send packets
            packet[0] = 0xFF;
            packet[1] = (unsigned char)(millis() >> 24);
            packet[2] = (unsigned char)((millis() << 8)>>24);
            packet[3] = (unsigned char)((millis() << 16)>>24);
            packet[4] = (unsigned char)((millis() << 24)>>24);
            for(int i = 0; i < 5; i++)
            {
                Serial1.print(packet[i]);
            }
        }
        break;

    case increaseOperatingPoint:
        {
            motorControl.operatingPoint += 1;
            
            #ifdef serialDebug
                #ifdef rx_txDebug
                    Serial.print("Received increase operating point: ");
                    Serial.println(motorControl.operatingPoint);
                #endif
            #endif
        }
        break;

    case decreaseOperatingPoint:
        {
            motorControl.operatingPoint -= 1;

            #ifdef serialDebug
                #ifdef rx_txDebug
                    Serial.print("Received decrease operating point: ");
                    Serial.println(motorControl.operatingPoint);
                #endif
            #endif
        }
        break;
		
    case increaseP:
	{
	    PID_GAINS[pitch].setP += 0.05;
	    PID_GAINS[roll].setP += 0.05;
			
	    #ifdef serialDebug
                #ifdef rx_txDebug
                    Serial.print("Received increase P: ");
                    Serial.println(PID_GAINS[pitch].setP);
                #endif
            #endif
	}
	break;

    case activateAltitudeHold:
	{
	    altitudeHold = true;
            initializePID(&altitudePID);
            targetAltitude = kinematics.altitude;
            
	    #ifdef serialDebug
                #ifdef rx_txDebug
                    Serial.print("Received turn on altitude hold");
                #endif
            #endif
	}
	break;
    
    case deactivateAltitudeHold:
	{
	    altitudeHold = false;
            initializePID(&altitudePID);

	    #ifdef serialDebug
                #ifdef rx_txDebug
                    Serial.print("Received turn off altitude hold");
                #endif
            #endif
	}
	break;
    
    case decreaseP:
	{
	    PID_GAINS[pitch].setP -= 0.05;
	    PID_GAINS[roll].setP -= 0.05;
			
	    #ifdef serialDebug
                #ifdef rx_txDebug
                    Serial.print("Received decrease P: ");
                    Serial.println(PID_GAINS[pitch].setP);
                #endif
            #endif
	}
	break;
		
    case increaseI:
	{
    	    PID_GAINS[pitch].setI += 0.05;
    	    PID_GAINS[roll].setI += 0.05;
    			
    	    #ifdef serialDebug
                #ifdef rx_txDebug
                    Serial.print("Received increase I : ");
                    Serial.println(PID_GAINS[pitch].setI);
                #endif
            #endif
	}
	break;
		
    case decreaseI:
        {
            PID_GAINS[pitch].setI -= 0.05;
            PID_GAINS[roll].setI -= 0.05;
    			
            #ifdef serialDebug
                #ifdef rx_txDebug
                    Serial.print("Received decrease I: ");
                    Serial.println(PID_GAINS[pitch].setI);
                #endif
            #endif
        }
        break;
	
    case increaseD:
        {
            PID_GAINS[pitch].setD += 0.05;
            PID_GAINS[roll].setD += 0.05;
			
            #ifdef serialDebug
                #ifdef rx_txDebug
                    Serial.print("Received increase D: ");
                    Serial.println(PID_GAINS[pitch].setD);
                #endif
            #endif
	}
	break;
		
    case decreaseD:
	{
	    PID_GAINS[pitch].setD -= 0.05;
	    PID_GAINS[roll].setD -= 0.05;
			
	    #ifdef serialDebug
                #ifdef rx_txDebug
                    Serial.print("Received decrease D: ");
                    Serial.println(PID_GAINS[pitch].setD);
                #endif
            #endif
	}
	break;

    case increasePitch:
        {
            double newSetpoint = incrementSetpoint(&pitchPID, 1);

            #ifdef serialDebug
                #ifdef rx_txDebug
                            Serial.print("Received increase pitch: ");
                            Serial.println(newSetpoint);
                #endif
            #endif
        }
        break;


    case decreasePitch:
        {
            double newSetpoint = incrementSetpoint(&pitchPID, -1);

            #ifdef serialDebug
                #ifdef rx_txDebug
                            Serial.print("Received decrease pitch: ");
                            Serial.println(newSetpoint);
                #endif
            #endif
        }
        break;

    case increaseRoll:
        {
            double newSetpoint = incrementSetpoint(&rollPID, 1);

            #ifdef serialDebug
                #ifdef rx_txDebug
                            Serial.print("Received increase roll: ");
                            Serial.println(newSetpoint);
                #endif  
            #endif
        }
        break;

    case decreaseRoll:
        {
            double newSetpoint = incrementSetpoint(&rollPID, -1);

            #ifdef serialDebug
                #ifdef rx_txDebug
                            Serial.print("Received decrease roll: ");
                            Serial.println(newSetpoint);
                #endif        
            #endif
        }
        break;

    case resetPitchRoll:
        {
            // Reset the values we are holding onto.
            pitchPID.setIntegratedError = 0;
            rollPID.setIntegratedError = 0;


            #ifdef NESTED_PID
                        rollPID.rateIntegratedError = 0;
                        pitchPID.rateIntegratedError = 0;
                        kinematics.pitchRate = 0;
                        kinematics.rollRate = 0;
            #endif

            kinematics.pitch = 0;
            kinematics.roll = 0;
            kinematics.rollRate = 0;

            #ifdef serialDebug
                #ifdef rx_txDebug
                            Serial.println("Received reset Pitch and Roll command! ");                          
                #endif
            #endif

            break;
        }
    }
}
/*=========================================================================
 processBatteryAlarms
 Watches for battery voltage alarms
 -----------------------------------------------------------------------*/
void processBatteryAlarms()
{
    if(softAlarm && !criticalAlarm)
    {
        // Auto Land
    }
    if(criticalAlarm)
    {
        motorControl.motorDISARM();
        while(true);
    }
}

/*=========================================================================
 PID_init()
 - Initializes the PID controllers
 -----------------------------------------------------------------------*/
void PID_init()                                          
{

    initializePID(&pitchPID);
    initializePID(&rollPID);
    initializePID(&yawPID);
    initializePID(&altitudePID);

    #ifdef serialDebug
        #ifdef NESTED_PID
            Serial.println(SET_ATT_KP);
            Serial.println(SET_ATT_KI);
        #endif
        #ifdef SINGLE_PID
            Serial.println(ATT_KP);
            Serial.println(ATT_KI);
            Serial.println(ATT_KD);
        #endif
    #endif

}
/*=========================================================================
 logData
 - Writes various data to the flight txt
 -----------------------------------------------------------------------*/
void logData()
{
    if (logFile)
    {
        // Log something
        logFile.print(millis());
        logFile.print(',');
        logFile.print(kinematics.altitude);
        logFile.print(',');
        logFile.print(targetAltitude);
        logFile.print(',');
        logFile.print(kinematics.climbRate);
        logFile.print(',');
        logFile.print(altitudePID.output);
        logFile.print(',');
        logFile.println(altitudePID.setpoint);
    }
    else
    {
        //Serial.println("Error opening file!");
    }
}

/*=========================================================================
 logFileStart
 - Initializes a .txt on the uSD
 -----------------------------------------------------------------------*/
void logFileStart()
{
    #ifdef serialDebug
        #ifdef sdDebug
            Serial.println("----Initializing .txt");
        #endif
    #endif

    pinMode(SS, OUTPUT);

    if (!SD.begin(SS)) 
    {
        #ifdef serialDebug
            #ifdef sdDebug
                    Serial.println("--------Initialization failed!");
            #endif
        #endif

        statusLED(-1);
        return;
    }
	
    // If the file exists, we want to delete it. 
    if (SD.exists(logFilename))
    {
        SD.remove(logFilename);
    }
    
    // Open the file for writing, here just for a title.
    logFile = SD.open(logFilename, FILE_WRITE);

    // if the file opened okay, write to it:
    if (logFile) {
        logFile.println("-----OpenSourceQuad-----");
        logFile.println();
        logFile.print("Date: ");
        logFile.println(__DATE__);
        logFile.print("Time: ");
        logFile.println(__TIME__);
        logFile.print("Software version: ");
        logFile.print(softwareVersionMajor);
        logFile.print(".");
        logFile.println(softwareVersionMinor);
        logFile.print("Flight Number: ");
        logFile.println(flightNumber);
		logFile.println("Starting PID values: ");
		#ifdef SINGLE_PID
		logFile.print("P: "); logFile.print(ATT_KP);
		logFile.print("I: "); logFile.print(ATT_KI);
		logFile.print("D: "); logFile.println(ATT_KD);
		#endif
		#ifdef NESTED_PID
		logFile.print("P: "); logFile.print(SET_ATT_KP);
		logFile.print(" I: "); logFile.print(SET_ATT_KI);
		logFile.print(" D: "); logFile.print(SET_ATT_KD);
		logFile.print(" Vel feedforward "); logFile.print(RATE_ATT_KP);
		logFile.print(" Acc "); logFile.print(RATE_ATT_KI);
		logFile.print(" Jerk "); logFile.println(RATE_ATT_KD);
		#endif
        logFile.println("Runtime data: \n\n");
    } 
    else {
        // if the file didn't open, print an error:
    #ifdef serialDebug
        #ifdef sdDebug
                Serial.println("--------Error opening file!");
        #endif
    #endif
    }

    logFile.close();

}

/*=========================================================================
 barometerInit
 - Initializes the barometer
 -----------------------------------------------------------------------*/
long barometerInit()
{
    // Take 10 readings of altitude to calibrate
    long initialAltitude, result;
    int count;
    for(int i = 0; i<60; i++)
    {
        barometer.updatePTA();
        delay(35); // Delay 35 ms for ADC
        if(barometer.conversionStep == 1)
        {
            initialAltitude += 1000*barometer.altitude;
            count++;
        }
    }
    result = initialAltitude / count;
    return result;
}

/*=========================================================================
 -----------------------------------------------------------------------*/
/*=========================================================================
 ******************************* Main Setup *******************************
 -----------------------------------------------------------------------*/
 /*=========================================================================
 -----------------------------------------------------------------------*/
void setup()
{ 
    delay(100); // Power supply, and various chip boot times

    #ifdef serialDebug
        Serial.begin(115200); 
        Serial.println();
    #endif

    Wire.begin();

    // Initialize various LED outputs
    pinMode(GREEN_LED1, OUTPUT);
    pinMode(GREEN_LED2, OUTPUT);
    pinMode(GREEN_LED3, OUTPUT);
    pinMode(YELLOW_LED1, OUTPUT);
    pinMode(YELLOW_LED2, OUTPUT);
    pinMode(YELLOW_LED3, OUTPUT);
    digitalWrite(GREEN_LED1, LOW);
    digitalWrite(GREEN_LED2, LOW);
    digitalWrite(GREEN_LED3, LOW);
    digitalWrite(YELLOW_LED1, LOW);
    digitalWrite(YELLOW_LED2, LOW);
    digitalWrite(YELLOW_LED3, LOW);

    /*****************************/
    /* Initialize EEPROM */
    /*****************************/

    statusLED(4);

    // Use the previously stored sensor offset values
    #ifdef usePreviousOffsets
        sensor_offs_t accelOffsets;
        sensor_offs_t gyroOffsets;
        
        readEEPROMOffsets(0, &accelOffsets);
        readEEPROMOffsets(1, &gyroOffsets);
        
        kinematics.io_ax = accelOffsets.x/1000.;
        kinematics.io_ay = accelOffsets.y/1000.;
        kinematics.io_az = accelOffsets.z/1000.;
        
        kinematics.io_wx = gyroOffsets.x/1000;
        kinematics.io_wy = gyroOffsets.y/1000;
        kinematics.io_wz = gyroOffsets.z/1000;
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
void loop()                          
{	
    // Check if we have enough time to safely do non-critical processes
    static bool priority = true;

    if(priority)
    {
        statusLED(4);
        fastTask();
	priority = false;
        statusLED(1);
    }
    else priority = true;

    // 70 Hz process
    if(micros() - t_70Hz >= _70HzPeriod && !priority)
    {
        statusLED(4);
        _70HzTask(); // 2000 us
	priority = true;
        statusLED(1);
    }

    // 20 Hz process
    if(micros() - t_20Hz >= _20HzPeriod && !priority)
    {
        statusLED(4);
        _20HzTask();
	priority = true;
        statusLED(1);
    }

    // 10 Hz process
    if(micros() - t_10Hz  >= _10HzPeriod && !priority)
    {
        statusLED(5);
        _10HzTask();
	priority = true;
        statusLED(2);
    }

    // 1 Hz process
    if(micros() - t_1Hz  >= _1HzPeriod && !priority)
    {
        statusLED(6);
        _1HzTask();
	priority = true;
        statusLED(3);
    }

    scanTelemetry();
    heartbeat();

    // Track the number of elapsed cycles
    cycleCount++;
}
/**! @ END MAIN CONTROL LOOP. @ !**/

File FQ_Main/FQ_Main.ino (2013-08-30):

 /*=========================================================================
 
*//*//*   FreeQuad   *//*//*
Name: FQ_Main.ino
Authors: Brandon Riches
         With some help from: Branden Yue, Andrew Coulthard
Date: 2013


TODO:
1) Chebyshev filter. 
2) Fix gyro DC drift. (Measure over time, possibly)
3) Tune PID using ZieglerÃ¢â‚¬â€œNichols method
        
Copyright stuff from all included libraries that I didn't write

  I2C.h   - I2C library
  Copyright (c) 2011-2012 Wayne Truchsess.  All right reserved.
  
  PID Library
  Brett Beauregard, br3ttb@gmail.com
  
  Adafruit_GPS
  
  Servo
  
  SoftwareSerial
  
  Wire
  
  SD
    -----------------------------------------------------------------------*/
#include <FQ_QuadGlobalDefined.h>
#include <FQ_Kinematics.h>
#include <FQ_SENSORLIB.h>
#include <FQ_Quadcopter.h>
#include <FQ_Motors.h>

#include <Adafruit_GPS.h>
#include <SoftwareSerial.h>
#include <PID_v1.h>
#include <I2C.h>
#include <Wire.h>
#include <Servo.h>
#include <SD.h>

File logfile;

/*=========================================================================
    Classes and important structures
    -----------------------------------------------------------------------*/
SENSORLIB_accel   	accel;
SENSORLIB_mag	  	mag;
SENSORLIB_gyro         	gyro;
fourthOrderData   	fourthOrderXAXIS,
			fourthOrderYAXIS,
			fourthOrderZAXIS;
kinematicData	  	kinematics;
FQ_MotorControl   	motorControl;

/*=========================================================================
    PID output variables and desired setpoints, and settings
    -----------------------------------------------------------------------*/
/*=========================================================================
    State variables
    - The program didnt like having these in the class.
    -----------------------------------------------------------------------*/
// PID output for alpha and beta, PID setpoint vars for alpha and beta
double set_a, pitchPID_out; 		  
double set_b, rollPID_out;	

// Sample time for PID controllers in ms	      	
int PID_SampleTime = 10;

// Constructors for the PID controllers
// The 4th, 5th, and 6th args in the constructors are, respectively:
// - Proportional gain
// - Integral gain
// - Derivative gain
#define Kp 1.500    
#define Ki 2.0    
#define Kd -0.0070
PID aPID(&kinematics.pitch,  &pitchPID_out,  &set_a,   Kp,  Ki,  Kd,  DIRECT);
PID bPID(&kinematics.roll,   &rollPID_out,  &set_b,   Kp,  Ki,  Kd,  DIRECT);


/*=========================================================================
    Function declarations
    -----------------------------------------------------------------------*/
void PID_init();           
boolean XBee_read();
int XBee_send(String data);
void get_telemetry(double* set_a, double* set_b);
void logfileStart();


/*=========================================================================
    Main Setup
    -----------------------------------------------------------------------*/
void setup()
{ 
  // Initialize the main serial UART for output. 
  Serial.begin(19200); 
  
  Serial.println(" ");
  
  // Initialize these pins for digital output.
  // They are used in the ERROR_LED function
  // Use ERROR_LED(1) for success,
  //     ERROR_LED(2) for warnings,
  //     ERROR_LED(3) for critical fail (has a while(1)).
  pinMode(GREEN_LED,   OUTPUT);
  pinMode(YELLOW_LED,  OUTPUT);
  pinMode(RED_LED,     OUTPUT);
  digitalWrite(GREEN_LED, LOW);
  digitalWrite(YELLOW_LED, LOW);
  digitalWrite(RED_LED, LOW);
  
  // Turn on the yellow LED to signify start of setup
  ERROR_LED(2);
  
  // Open a .txt file for data logging and debugging
  logfileStart();
    
  // Initialize the sensors.
  // Sensors include: 
  //   - Gyro (InvenSense MPU3050)
  //   - Accel/Magnetometer (LSM303)
  //   - USRF
  //   - GPS module (Adafruit Ultimate)
  //   - RTC Module
  while(!initSensor(accel, 
                    mag, 
                    gyro,
                    &kinematics));
  
  // Initialize the PID controllers. This is a sub-function, below loop.
  PID_init();   
  
  // Initialize motors. This turns the motors on, and sets them all to a speed
  // just below take-off speed.
  // Enter a %, from 0 - 100
  ERROR_LED(2);
  motorControl.calibrateESC();
  motorControl.startMotors();
  delay(50);
  
  // Set both the alpha and beta setpoints to 0. 
  set_a = 0;		               
  set_b = 0;  
  
  // Initialize the fourth order struct
  setupFourthOrder(&fourthOrderXAXIS,
                   &fourthOrderYAXIS,
                   &fourthOrderZAXIS);
  ERROR_LED(1);    
}

/*=========================================================================
    MAIN CONTROL LOOP
    -----------------------------------------------------------------------*/
void loop()                          
{
  // This is the main runtime function included in the Quadcopter class.
  //
  // It includes a number of different priorities, based on the time elapsed
  // since it was last called (This is because various sensors or events may
  // have different time intervals between them). 
  // 
  // In the most basic priority, the function gathers new magnetometer, 
  // accelerometer, and gryo data. It then runs a basic moving average on these
  // data to smooth them. Then, it uses a complementary filter to help obtain 
  // more accurate readings of angle
  mainProcess(pitchPID_out, 
              rollPID_out, 
              &accel, 
              &mag, 
              &gyro,
              &kinematics,
              &fourthOrderXAXIS,
              &fourthOrderYAXIS,
              &fourthOrderZAXIS,
              &motorControl);  
        
  // Updates the PID controllers. They return new outputs based on current
  // and past data. These outputs are used to decide what the motor speeds should be set to.
  if (millis() > 4000)
  {
    aPID.Compute();
    bPID.Compute();
  }  
  // We print all the data to the SD logfile, for debugging purposes. 
  // Once a completely working build is finished, this may or may not be removed for
  // the sake of speed.
  logfile = SD.open("run_log.txt", FILE_WRITE);
  if (logfile)
  {
    logfile.print(micros());
    logfile.print(",");
    logfile.print(kinematics.pitch);
    logfile.print(",");
    logfile.print(kinematics.roll);
    logfile.print(",");
//    logfile.print(motor1s);
//    logfile.print(",");
//    logfile.print(motor2s);
//    logfile.print(",");
//    logfile.print(motor3s);
//    logfile.print(",");
//    logfile.print(motor4s);
//    logfile.print(",");
    logfile.print(pitchPID_out);
    logfile.print(",");
    logfile.println(rollPID_out);
  }
  logfile.close();
  
  // Close the file after sometime  of logging.
  if (millis() >= 60000)
  {
    motorControl.motorDISARM();
    ERROR_LED(3);
  }

 // Serial.println(motorControl.motorSpeeds.m1_DC);

  
}
/**! @ END MAIN CONTROL LOOP. @ !**/
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

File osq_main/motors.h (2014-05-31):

/*=====================================================================
     Motors library
     OpenSourceQuad
     -------------------------------------------------------------------*/
/*================================================================================
 
     Author		: Brandon Riches
     Date		: August 2013
     License		: GNU Public License
     
     Implements an atomicPWM control of different motor configurations for the
     atmega2560 uC
     
     Copyright (C) 2013  Brandon Riches
     
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
     -----------------------------------------------------------------------------*/

#ifndef MOTORS_H_INCLUDED
#define MOTORS_H_INCLUDED

#if ARDUINO >= 100
    #include "Arduino.h"
#else
    #include "WProgram.h"
#endif

#define USE_300HZ_PWM 
#define USE_4MOTORS

#ifdef USE_150HZ_PWM
    #define PWM_FREQUENCY   150
#endif

#ifdef USE_200HZ_PWM
    #define PWM_FREQUENCY   200
#endif

#ifdef USE_250HZ_PWM
    #define PWM_FREQUENCY   250
#endif

#ifdef USE_300HZ_PWM
    #define PWM_FREQUENCY   300
#endif

#ifdef USE_400HZ_PWM
    #define PWM_FREQUENCY   400
#endif

#define PRESCALER		8
#define PWM_COUNTER_PERIOD	(F_CPU/PRESCALER/PWM_FREQUENCY)


#define MIN_COMMAND      	1075     // the shortest pulse
#define MAX_COMMAND     	1600     // the longest pulse

#define _PLUSconfig

//#define _Xconfig			1

enum {motor1, motor2, motor3, motor4, motor5, motor6, motor7, motor8};

int motorSpeeds[8] = {
    0, 0, 0, 0, 0, 0, 0, 0};

void initializePWM()
{
    // Using counters 3 and 4
    // These are 16bit counter registers
    DDRE = DDRE | B00111000;			// Set PE3-5, OC3A, OC3B, OC3C to outputs
    DDRH = DDRH | B00001000;			// Set PH3, OC4A to outputs

    // Init PWM Timer 3                                       // WGMn1 WGMn2 WGMn3  = Mode 14 Fast PWM, TOP = ICRn ,Update of OCRnx at BOTTOM
    TCCR3A = (1<<WGM31)|(1<<COM3A1)|(1<<COM3B1)|(1<<COM3C1);  // Clear OCnA/OCnB/OCnC on compare match, set OCnA/OCnB/OCnC at BOTTOM (non-inverting mode)
    TCCR3B = (1<<WGM33)|(1<<WGM32)|(1<<CS31);                 // Prescaler set to 8, that gives us a resolution of 0.5us
    ICR3 = PWM_COUNTER_PERIOD;                                // Clock_speed / ( Prescaler * desired_PWM_Frequency) #defined above.

    // Init PWM Timer 4
    TCCR4A = (1<<WGM41)|(1<<COM4A1);
    TCCR4B = (1<<WGM43)|(1<<WGM42)|(1<<CS41);
    ICR4 = PWM_COUNTER_PERIOD;
};

void writeMotors()
{
    OCR3A = motorSpeeds[motor1] * 2;
    OCR3B = motorSpeeds[motor2] * 2;
    OCR3C = motorSpeeds[motor3] * 2;
    OCR4A = motorSpeeds[motor4] * 2;
};

void commandAllMotors(int speed)
{
    motorSpeeds[motor1] = speed;
    motorSpeeds[motor2] = speed;
    motorSpeeds[motor3] = speed;
    motorSpeeds[motor4] = speed;
    motorSpeeds[motor5] = speed;
    motorSpeeds[motor6] = speed;
    motorSpeeds[motor7] = speed;
    motorSpeeds[motor8] = speed;

    writeMotors();
};

/** Main Class **/
class MotorControl
{
    public:
        MotorControl(int num = 4);
    
        // Function ideas //
        void calibrateESC(int numESC = 4);
        void motorDISARM();
        void startMotors();
        void updateMotors(double pitchPID, double rollPID, double yawPID, double elevPID);
    
        double changeOperatingPoint(double opChange);
    
        double operatingPoint;
    
    private:
        bool 	MOTORS_ARMED;
        bool	ESC_READY;
        int 	NUM_MOTORS;
    
    
        int 	passiveMIN;
        int	passiveMAX;

};

MotorControl :: MotorControl(int num)
{
    this->NUM_MOTORS 	= num;
    this->MOTORS_ARMED 	= false;
    this->ESC_READY		= false;
    this->passiveMIN	= MIN_COMMAND+25;
    this->passiveMAX	= MAX_COMMAND-100;
    this->operatingPoint    = 1200;
    commandAllMotors(this->operatingPoint);
};

void MotorControl :: calibrateESC(int numESC)
{
    initializePWM();

    this->MOTORS_ARMED = true;

    // Calibration procedure
    // TODO: calibrate ESC

    this->ESC_READY = true;
};

void MotorControl :: startMotors()
{
    if(this->ESC_READY)
    {
        #ifdef USE_4MOTORS
            for(int DC = 0; DC < MIN_COMMAND; DC += 10)
            {
                motorSpeeds[motor1] = DC;
                motorSpeeds[motor2] = DC;
                motorSpeeds[motor3] = DC;
                motorSpeeds[motor4] = DC;
                writeMotors();
                delay(20);
            }
    
            delay(100);
    
            motorSpeeds[motor1] = MIN_COMMAND+100;
            motorSpeeds[motor2] = MIN_COMMAND+100;
            motorSpeeds[motor3] = MIN_COMMAND+100;
            motorSpeeds[motor4] = MIN_COMMAND+100;
            writeMotors();
        #endif
    }
};

void MotorControl :: updateMotors(double p_pitchPID, double p_rollPID, double p_yawPID, double p_elevPID)
{
    double PID_scalar = 1;

    double rollPID = (p_rollPID) / PID_scalar;
    double pitchPID = (p_pitchPID) / PID_scalar;
    double yawPID = (p_yawPID) / PID_scalar;
    double elevPID = (p_elevPID) / PID_scalar;

    if (MOTORS_ARMED)
    {
        #ifdef _PLUSconfig
            #ifdef USE_4MOTORS
                    /* //Control pitch/roll */
                    motorSpeeds[motor1] = operatingPoint + pitchPID;
                    motorSpeeds[motor2] = operatingPoint - rollPID;
                    motorSpeeds[motor3] = operatingPoint + rollPID;
                    motorSpeeds[motor4] = operatingPoint - pitchPID;
            
                    /* //Control elevation */
                    operatingPoint += elevPID;
            #endif

            #ifdef USE_4MOTORS
                    /* //Control yaw */
                    motorSpeeds[motor1] += yawPID;        // CW
                    motorSpeeds[motor2] -= yawPID;
                    motorSpeeds[motor3] -= yawPID;        // CCW
                    motorSpeeds[motor4] += yawPID;
            #endif

            // Restrict duty cycle to max/min
            motorSpeeds[motor1] = constrain(motorSpeeds[motor1], passiveMIN, passiveMAX);
            motorSpeeds[motor2] = constrain(motorSpeeds[motor2], passiveMIN, passiveMAX);
            motorSpeeds[motor3] = constrain(motorSpeeds[motor3], passiveMIN, passiveMAX);
            motorSpeeds[motor4] = constrain(motorSpeeds[motor4], passiveMIN, passiveMAX);
            motorSpeeds[motor5] = constrain(motorSpeeds[motor5], passiveMIN, passiveMAX);
            motorSpeeds[motor6] = constrain(motorSpeeds[motor6], passiveMIN, passiveMAX);
            motorSpeeds[motor7] = constrain(motorSpeeds[motor7], passiveMIN, passiveMAX);
            motorSpeeds[motor8] = constrain(motorSpeeds[motor8], passiveMIN, passiveMAX);
    
            writeMotors();
        #endif

        #ifdef _Xconfig
        //TODO:
        // Write motor logic for X config
        #endif
    }
};

// Used to manually control altitude.
double MotorControl :: changeOperatingPoint(double opChange)
{
    operatingPoint += opChange;
    constrain(operatingPoint, 1200, 1450);
    return operatingPoint;
};
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

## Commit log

2013-05-09 Added I2C library
2013-05-09 Added Adafruit_LSM303DLHC Driver
    Forked from adafruit
2013-05-13 Fixed bug.
    File is now functional for returning data in the correct, noise filtered
    format.
    Work on integration begins...
2013-05-18 Create Motor Button Control
    Pin 9 is the servo output for the motor.
    Pin 7/8 are button inputs where 7 will increase the speed of the motor and 8 will decrease the speed.
    There is a fail-safe for both the upper and lower limits of when the motor will turn on ... based on trial and error, though I didn't have the propeller attached. These values may change.
2013-05-19 Added x,y,z velocity/displacement
2013-05-20 Created InfraredDistanceTest
    Experimental thing with my Infrared proximity sensor... With it, we can
    get "fairly" accurate altitudes.
2013-05-24 Added public version of sensor struct
2013-05-24 Added infrared sensor measurements
2013-05-26 Added PID libraries
2013-05-27 PID initial working commit.
2013-06-03 Created Processing sketch for debug and filtering
    Upon discovery of excess noise, I have started working with Ken on a
    frequency domain analysis of the sensor output signal. Motor operation
    seems to introduce a high magnitude, high frequency component into the
    signal and it needs to be removed
    [Data_6_3_2013.csv, ax_nomotors.csv]
2013-06-07 Created new dir "Misc Files & Idea Box"
    Moved Whiteboard.cpp and MiscFunctions.cpp to this dir.
    [ERR_LOG.csv]
2013-06-07 Tweaks to functions.
    [ERR_LOG.csv]
2013-06-08 Added class DATABANK
    I expect that we'll never use it.
    [ERR_LOG.csv]
2013-06-08 Removed these two files; they were not used
    [Conversions&InfraredCal.xlsx]
2013-06-08 Moved PID to a subfunction
2013-06-15 Added a shit ton of stuff
    [LOGTEST.csv, LOGTEST1.csv]
2013-06-24 New code layout, new filenames
    Changed code strategy from class, to global functions. Doesn't work!
    [1M_75_T1.xlsx, M75_T1.xlsx]
2013-07-06 Updated motortest
2013-07-07 Added Status LEDS, added compatability w/ SENSORLIB
2013-07-09 Added MAG functionality to SENSORLIB
2013-07-10 Added some magnetometer functions, create I2cBusTester
2013-08-04 Added Chebyshev filter. Issues exist still, WIP
2013-08-05 Added QuadSim
    [Data.csv]
2013-08-10 Large number of changes
    - Changed the format of SENSORLIB; it now closely matches the Adafruit
    library
    - Changed the way we were implementing the fourth order filter, it now
    should work.
    - Changed various formatting in Quadcopter.h
2013-08-10 Removed two libraries
    SdFat and LedCube
2013-08-10 Cleaned up the Libraries folder, added QuadGlobalDefined.h
    [1M_75_T1.xlsx, LOGTEST.csv, LOGTEST1.csv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]
2013-08-10 Removed "QuadcopterDebug"
    [Data_6_3_2013.csv, ax_nomotors.csv]
2013-08-29 New code format under construction
    - Moved classes and structures to global scope
    - Created kinematics header to increase abstraction in the main runtime
2013-08-30 Fixed a bunch of bugs, completed new format
    [FQ_Main.ino]
2013-08-30 Completed change over to new format
    - Fixed library links
    - Fixed gyro sensor readouts by adding it to SENSORLIB
    - Modified PID
    [FQ_Main.ino]
2013-09-01 Got serious about tuning the PID
2013-09-02 Started hardware PWM lib
2013-09-03 Fixed the altitude processor
    [OSQ_Main.ino]
2013-09-05 altitudeProcessor now controls the power of the USRF
2013-09-14 Added PID library, some bug fixes
    [OSQ_Main.ino, OSQ_Motors.h, OSQ_PID.h]
2013-09-15 Kalman Filter Update
    Added kalman filter library to git for testing
2013-09-30 Some attempts to fix PID algorithm other fixes
    [BarometerTest.ino, BaseStation.ino, BatteryVoltageMonitor.ino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]
2013-10-01 Fixed some fairly obvious errors, tuning may actually be possible now.
    [OSQ_Main.ino, OSQ_Motors.h, OSQ_PID.h]
2013-10-26 Kalman Filter Header
    This is a filter for kalmans
2013-10-29 Added the option to switch between single/nested PID
2013-11-03 Kalman Filter Code
    This is the Kalman Filter header that may or may not work as intended.
2013-11-03 Revert "Kalman Filter Code"
    This reverts commit 79ce451de3c8acbbd1afc64fec2fe551ac1fd8bc.
2013-11-05 Big update to PID, fixed nested/single
    Works pretty well, is much more optimized than before
    [OSQ_Main.ino, OSQ_Motors.h, OSQ_PID.h]
2013-11-13 Removed accelerometer from control loop, found transfer function
    [MomentOfInertia and Mass.xlsx, NOV11_2013.xlsx]
2013-11-13 Cleaning up some old files
    [ERR_LOG.csv]
2013-11-14 Using the kalman filter, added in a typedef to make it easier
2013-11-15 First stable PID and radio control
    I threw it into the air and it was stable.
2013-11-26 Queue Library
    Arduino data type fixes
2013-12-02 Kalman filter replaced by complementary
    I feel like I'm smacking my head against a wall with this thing.
    [OSQ_Main.ino, OSQ_PID.h, OSQ_Quadcopter.h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]
2013-12-06 Some commenting
    [MomentOfInertia and Mass.xlsx]
2013-12-12 Bug fixes, timing, some sensor fixes, PID coefficients
    [OSQ_BMP085.h, OSQ_BatteryMonitor.h, OSQ_EEPROM.h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]
2013-12-21 Some more timing and sensor changes. Things seem good
    If I could control it better, I feel like it could fly with some
    stability now.
    [BaseStationUI.pde, OSQ_Main.ino, OSQ_Motors.h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]
2014-03-24 She's as stable as your favourite stable thing now.
    [Torque.xlsx]
2014-04-01 Better startup safety, logfile names, PID coeffs
2014-04-03 Work on yaw control, now that pitch and roll are good
2014-04-07 Control PID from basestation, upped control frequency
2014-04-07 Complementary filter improved, drift eliminated
    [OSQ_PID.h]
2014-04-11 New class for calculating variance of pitch/roll
2014-04-18 Cleaned up kinematics and added comments
2014-05-01 New board up and running on the quad.
    Changed lots of different stuff to work with the new board, and added
    some standard hardware tests
2014-05-04 Altitude hold in the works
    [Torque.xlsx]
2014-05-13 Added pcb schematics
    [FlightControl.brd, FlightControl.sch, bom.xlsx]
2014-05-25 Updated schematics
    [FlightControl.brd, FlightControl.sch, bom.xlsx]
2014-07-07 lots of small stuff
    [FlightControl.brd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]

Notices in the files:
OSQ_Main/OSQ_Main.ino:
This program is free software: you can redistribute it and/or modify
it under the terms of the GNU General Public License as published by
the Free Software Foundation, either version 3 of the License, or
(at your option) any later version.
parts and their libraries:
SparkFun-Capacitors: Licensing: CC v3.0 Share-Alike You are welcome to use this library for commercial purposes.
